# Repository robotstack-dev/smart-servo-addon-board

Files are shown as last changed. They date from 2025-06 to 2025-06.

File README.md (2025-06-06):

# Smart Servo Add-on Board

This repository contains the hardware design files and documentation for the Smart Servo Add-On Board.

[**Buy on Tindie**](https://www.tindie.com/products/robotstack/smart-servo-addon-board/)

> **Note:** This is an early version of the board. While it has been tested with several servo models, bugs may exist. Please report any issues you encounter.

## Description

This board allows wireless control different TTL smart servos. I developed it to use with Seeed's Xiao esp32-s3 Microcontroller, but it should also work with Adafruit's QT-Py esp32-s3, and likely other esp32s. I've tested it with the following smart servos: Robotis XL430-W250, AX-12W, Feetech HL3930M, and briefly with Waveshare's ST3215. Firmware and Control Software are available in the links below.

<div style="text-align: center;">
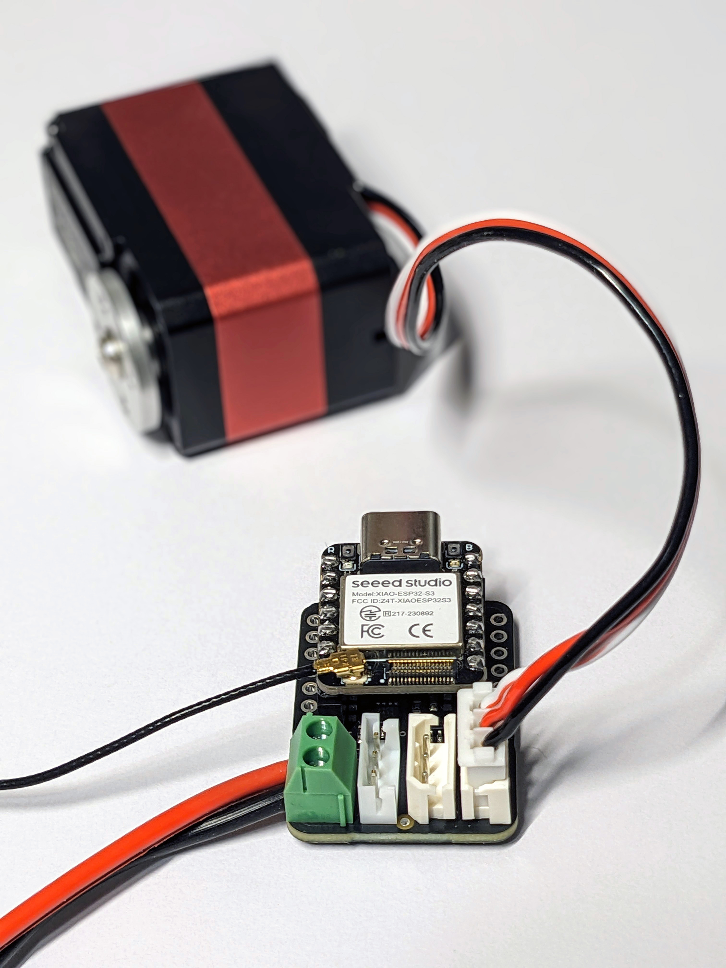
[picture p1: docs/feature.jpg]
Feature Image of Smart Servo Add-on Board
    
</div>

## Features

- Wireless Control of Smart Servos
- Compatible with Seeed Xiao and Adafruit QT-Py Form Factor
- Connectors for:

  - Dynamixel X-Series
  - Dynamixel AX-Series
  - Feetech HLS-Series / Waveshare ST3215

  > (Likely compatible with other smart servos; check your servo's specs)

- Stemma QT / QWIIC connector for compatible daughter boards (ie. sensors)
- Breakout pins
- 6.5 to 12 Volt Supply Range (check servo documentation for requirements)
- On board 5V regulator for Microcontroller
- Reverse Polarity Protection
- Firmware and Control Software available

## Hardware Overview

The pinouts are determined by the microcontroller you use. This board was designed to be used with the Seeed Xiao ESP32-S3 or the Adafruit QT Py ESP32-S3. See their documentation for details.

> **Important**: Check your servo connector's pinouts before connecting! Connecting to the wrong connector could damage the board and your servo.

<div style="text-align: center;">
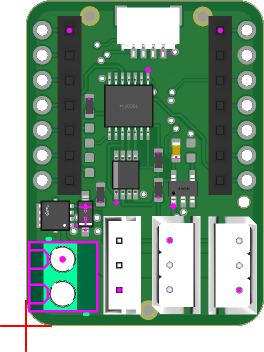
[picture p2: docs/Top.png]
Top View of Smart Servo Add-on Board
    
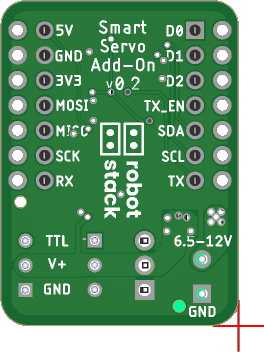
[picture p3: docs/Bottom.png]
Bottom View of Smart Servo Add-on Board
    
</div>

<div style="text-align: center;">
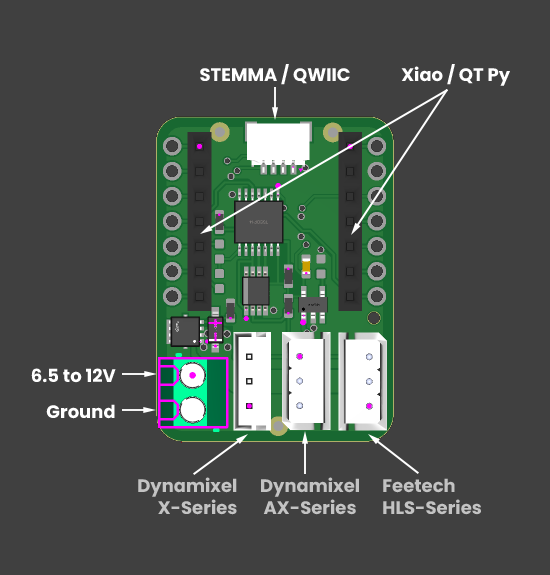
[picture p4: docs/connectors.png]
Connectors of Smart Servo Add-on Board
    
</div>

<div style="text-align: center;">
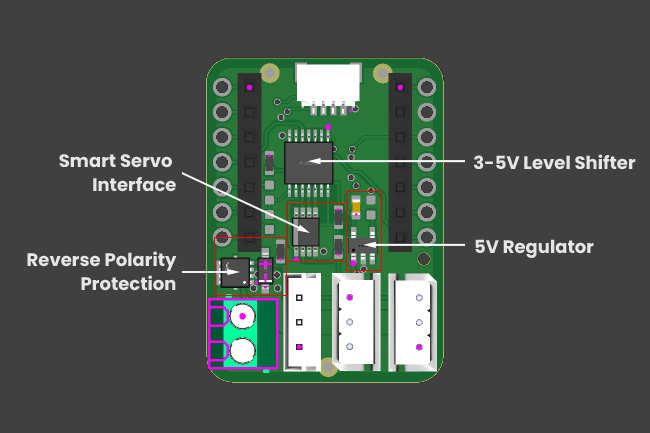
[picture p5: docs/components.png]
Components of Smart Servo Add-on Board
    
</div>

## Getting the Board

### Pre-assembled

Pre-assembled boards are available for purchase on Tindie:
[Buy on Tindie](https://www.tindie.com/products/robotstack/smart-servo-addon-board/)

### DIY

You can build this board yourself using the hardware design files in this repository.

## Firmware

Example firmware for this board is available in a separate Arduino library. You can find it here:
[Smart Servo Bridge](https://github.com/robotstack-dev/smart-servo-bridge)

The library can be used with or without this addon board, making it flexible for different applications.

## Control Software

Python SDKs enabling wireless control of your smart servos are available. They require use of these boards implementing the [Smart Servo Bridge](https://github.com/robotstack-dev/smart-servo-bridge) library, or similar:

- [FTServo Python Websockets](https://github.com/robotstack-dev/ftservo-python-websockets)
- [Dynamixel Python SDK Websockets](https://github.com/robotstack-dev/dynamixel-python-sdk-websockets)

Other smart servos will require similar modifications to their SDKs.

## Getting Started

1. Build or purchase the circuit.
2. Attach a Microcontroller (eg. Seeed Xiao esp32-s3, or Adafruit QT Py esp32-s3).
3. Upload firmware over USB.
4. Attach your smart servo to the correct connector, according to your servo pinout.
5. Attach a power supply between 6.5 and 12 Volts, according to your servo requirements.
6. Run one of the control software examples that corresponds with your servo.

## Contributing

Contributions are welcome! Here are some guidelines to help you get started:

### How to Contribute

1. Fork the repository and create your branch from `master`.
2. Clone your fork and make your changes.
3. Test your changes if possible.
4. Submit a pull request with a clear description of your changes.

### Code of Conduct

- Be respectful and considerate in your communications.
- Assume good intentions and be constructive in feedback.

### Reporting Issues

- Use the issue tracker to report bugs or request features.
- Provide as much detail as possible (steps to reproduce, expected behavior, etc.).

## Author

Nicholas Stedman

- [GitHub](https://github.com/nsted)
- [Tindie Store](https://www.tindie.com/stores/robotstack/)

## License

This project is licensed under the MIT License - see the [LICENSE.txt](LICENSE.txt) file for details.

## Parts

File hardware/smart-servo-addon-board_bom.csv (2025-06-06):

Comment | Designator | Footprint | LCSC Part #
1uf | C2 | C0603
2K | R6 R7 | R0603
9A/30V/15mΩ | Q1 | 8-POWERVDFN-3X3
10K | R1 R4 R5 R8 | R0603
10nf | C1 | C0603
22-03-5035 | J2 J5 | SHDR3W60P0X250_1X3_990X490X590
B3B-EH-A | J3 | SHDR3W64P0X250_1X3_1000X380X60
BZT52C15-7-F | Z1 | SOD3716X145N
FIDUCIAL"" | FD4 FD5 FD6 | FIDUCIAL_1MM
GREEN-2P-3.5 | J1 | H2-3.5-7.0X7.0MM
QWIIC_RA | J4 | JST04_1MM_RA
RS1-07-G
 | J6 J7 | 1X07
SN74LVC2G241DCTR | U4 | SOP65P400X130-8N
SPX3819M5_5_0 | U3 | SOT23-5
TXB0104PWR | U2 | TSSOP14
XIAO-THRUHOLE | U1 | XIAO-GENERIC-THRUHOLE-MODULE14P-2.54-21X17.8MM

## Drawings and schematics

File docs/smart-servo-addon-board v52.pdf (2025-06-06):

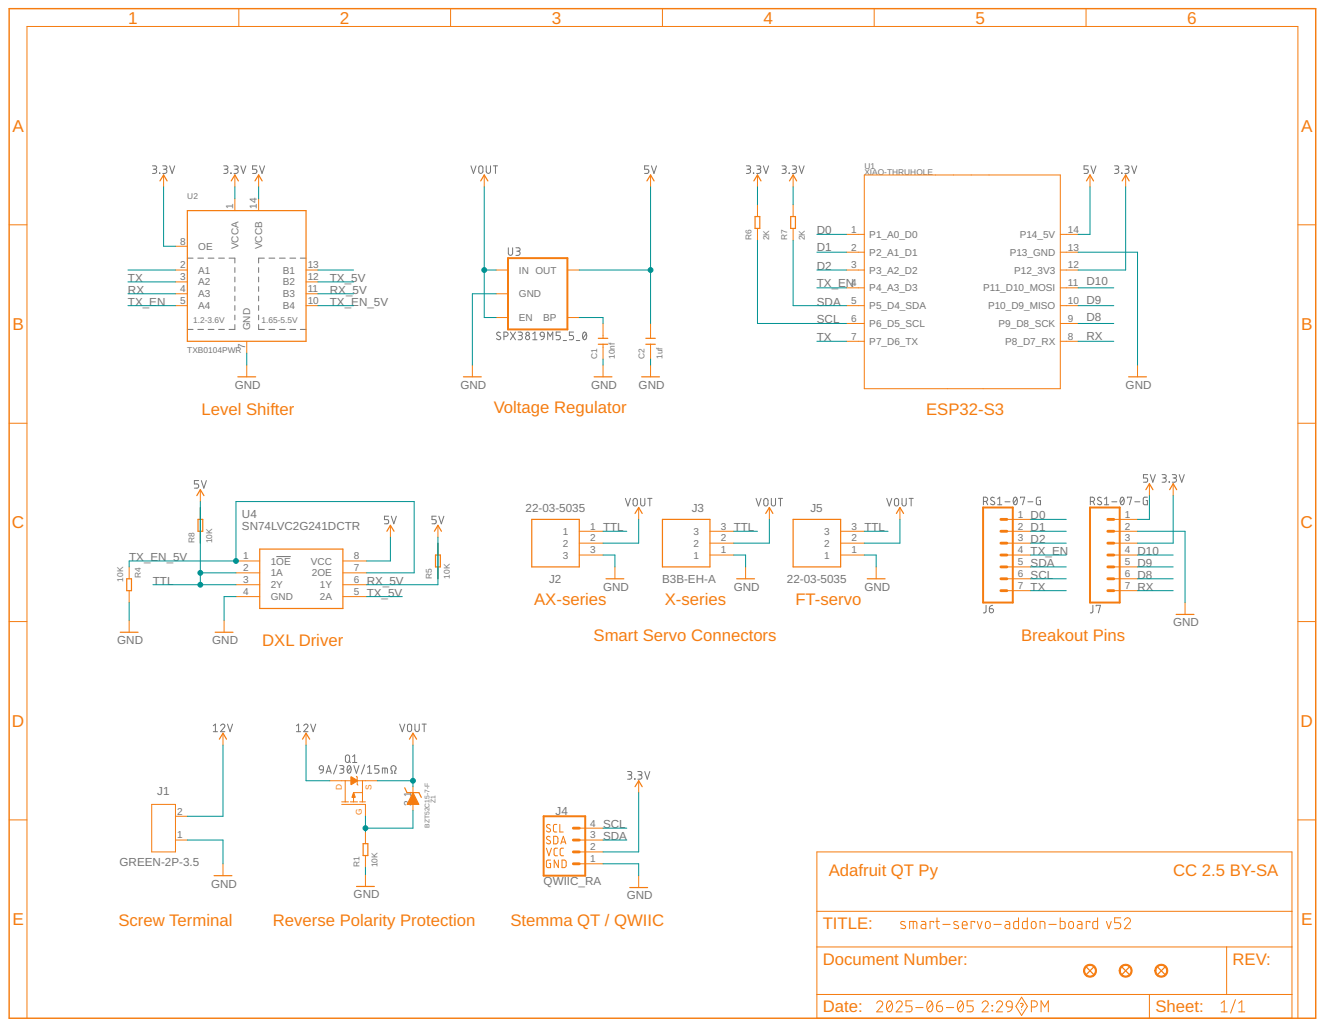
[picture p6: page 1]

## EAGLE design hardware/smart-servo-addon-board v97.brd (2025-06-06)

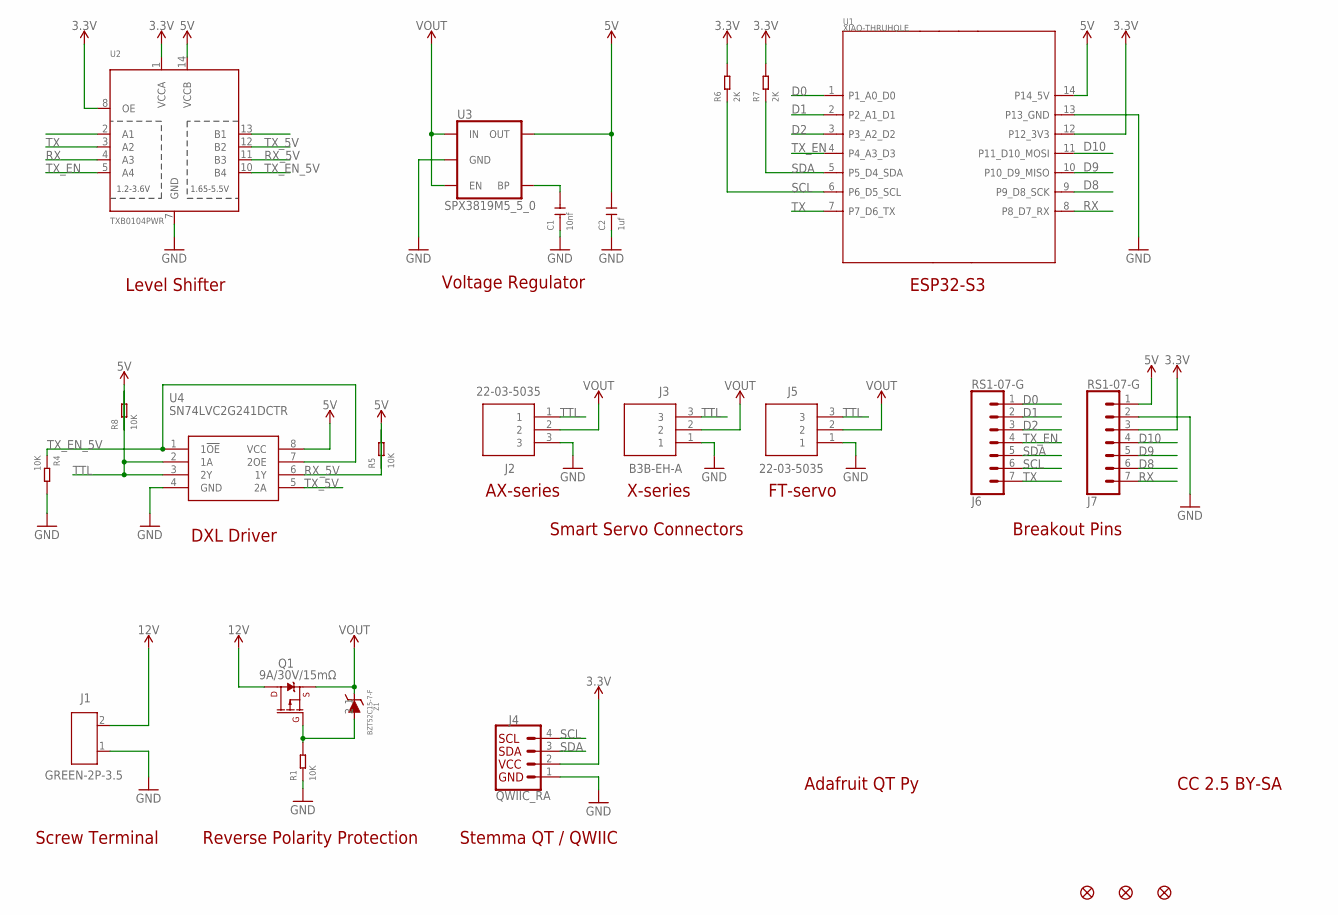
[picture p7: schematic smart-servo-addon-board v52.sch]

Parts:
C1: 10nf; C0603
C2: 1uf; C0603
FD4, FD5, FD6: FIDUCIAL""; FIDUCIAL_1MM
J1: GREEN-2P-3.5; H2-3.5-7.0X7.0MM
J2, J5: 22-03-5035; SHDR3W60P0X250_1X3_990X490X590
J3: B3B-EH-A; SHDR3W64P0X250_1X3_1000X380X60
J4: QWIIC_RA; JST04_1MM_RA
J6, J7: RS1-07-G; 1X07
Q1: 9A/30V/15mΩ; 8-POWERVDFN-3X3
R1, R4, R5, R8: 10K; R0603
R6, R7: 2K; R0603
U1: XIAO-THRUHOLE; XIAO-GENERIC-THRUHOLE-MODULE14P-2.54-21X17.8MM
U2: TXB0104PWR; TSSOP14
U3: SPX3819M5_5_0; SOT23-5
U4: SN74LVC2G241DCTR; SOP65P400X130-8N
Z1: BZT52C15-7-F; SOD3716X145N

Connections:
3.3V: J4.2, J7.3, R6.2, R7.2, U1.12 (P12_3V3), U2.1 (VCCA), U2.8 (OE)
5V: C2.2, J7.1, R5.1, R8.1, U1.14 (P14_5V), U2.14 (VCCB), U3.5 (OUT), U4.8 (VCC)
12V: J1.2, Q1.5@1 (D), Q1.5@2 (D), Q1.5@3 (D)
D0: J6.1, U1.1 (P1_A0_D0)
D1: J6.2, U1.2 (P2_A1_D1)
D2: J6.3, U1.3 (P3_A2_D2)
D8: J7.6, U1.9 (P9_D8_SCK)
D9: J7.5, U1.10 (P10_D9_MISO)
D10: J7.4, U1.11 (P11_D10_MOSI)
GND: C1.1, C2.1, J1.1, J2.3, J3.1, J4.1, J5.1, J7.2, R1.1, R4.2, U1.13 (P13_GND), U2.7 (GND), U3.2 (GND), U4.4 (GND)
unnamed: C1.2, U3.4 (BP)
unnamed: Q1.4 (G), R1.2, Z1.2 (A)
RX: J7.7, U1.8 (P8_D7_RX), U2.4 (A3)
RX_5V: R5.2, U2.11 (B3), U4.6 (1Y)
SCL: J4.4, J6.6, R6.1, U1.6 (P6_D5_SCL)
SDA: J4.3, J6.5, R7.1, U1.5 (P5_D4_SDA)
TTL: J2.1, J3.3, J5.3, R8.2, U4.2 (1A), U4.3 (2Y)
TX: J6.7, U1.7 (P7_D6_TX), U2.3 (A2)
TX_5V: U2.12 (B2), U4.5 (2A)
TX_EN: J6.4, U1.4 (P4_A3_D3), U2.5 (A4)
TX_EN_5V: R4.1, U2.10 (B4), U4.1 (1!OE), U4.7 (2OE)
VOUT: J2.2, J3.2, J5.2, Q1.1 (S), Q1.2 (S), Q1.3 (S), U3.1 (IN), U3.3 (EN), Z1.1 (K)

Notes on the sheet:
ESP32-S3
Smart Servo Connectors
Level Shifter
DXL Driver
Screw Terminal
Stemma QT / QWIIC
Voltage Regulator
Breakout Pins
X-series
FT-servo
AX-series
Reverse Polarity Protection
Adafruit QT Py
CC 2.5 BY-SA

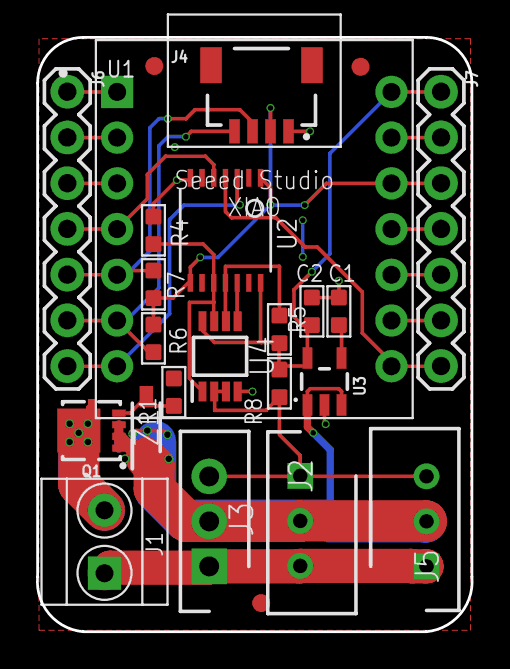
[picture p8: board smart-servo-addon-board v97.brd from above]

Board: 2 copper layers, 24.2 x 33.0 mm, 24 parts (0 on the bottom side), 22 nets.

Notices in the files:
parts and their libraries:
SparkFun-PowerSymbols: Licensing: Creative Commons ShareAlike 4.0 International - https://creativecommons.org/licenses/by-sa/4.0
